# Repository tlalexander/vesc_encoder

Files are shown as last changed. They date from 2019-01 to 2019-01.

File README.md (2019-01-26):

# vesc_encoder
An openly licensed magnetic encoder board, compatible with VESC 4.12 based designs.

The data in this repository is licensed CC0, which generally means "Public Domain".
https://creativecommons.org/publicdomain/zero/1.0/

In other words: this information can be used for any purpose.

# Screenshots

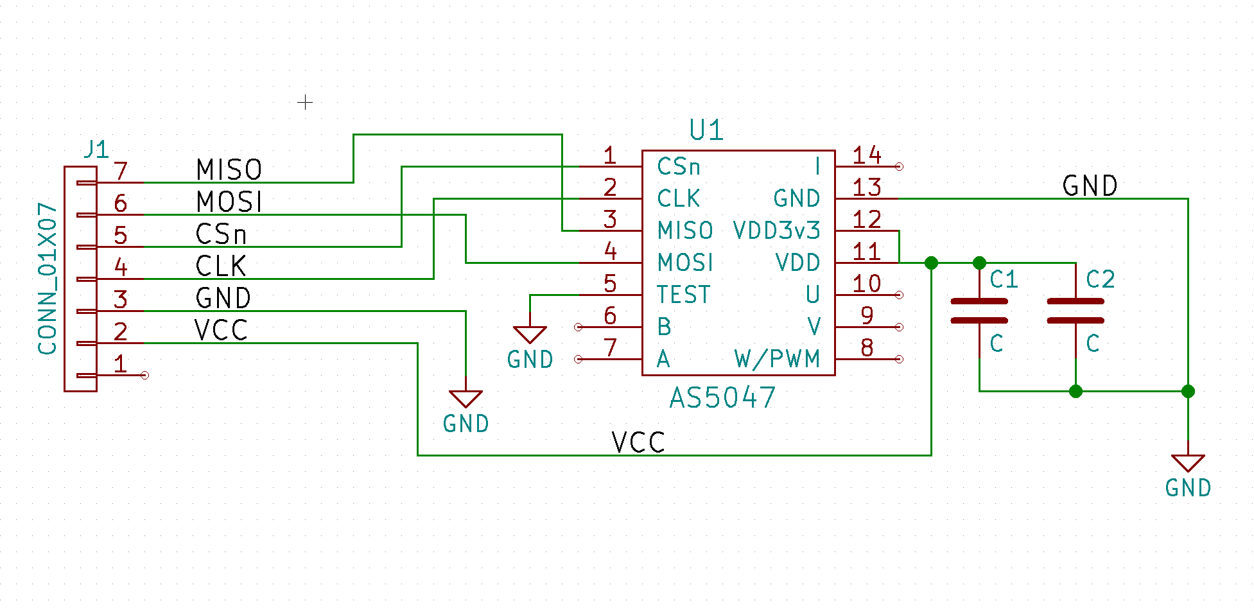
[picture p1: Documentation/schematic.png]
Image of Schematic Schematic

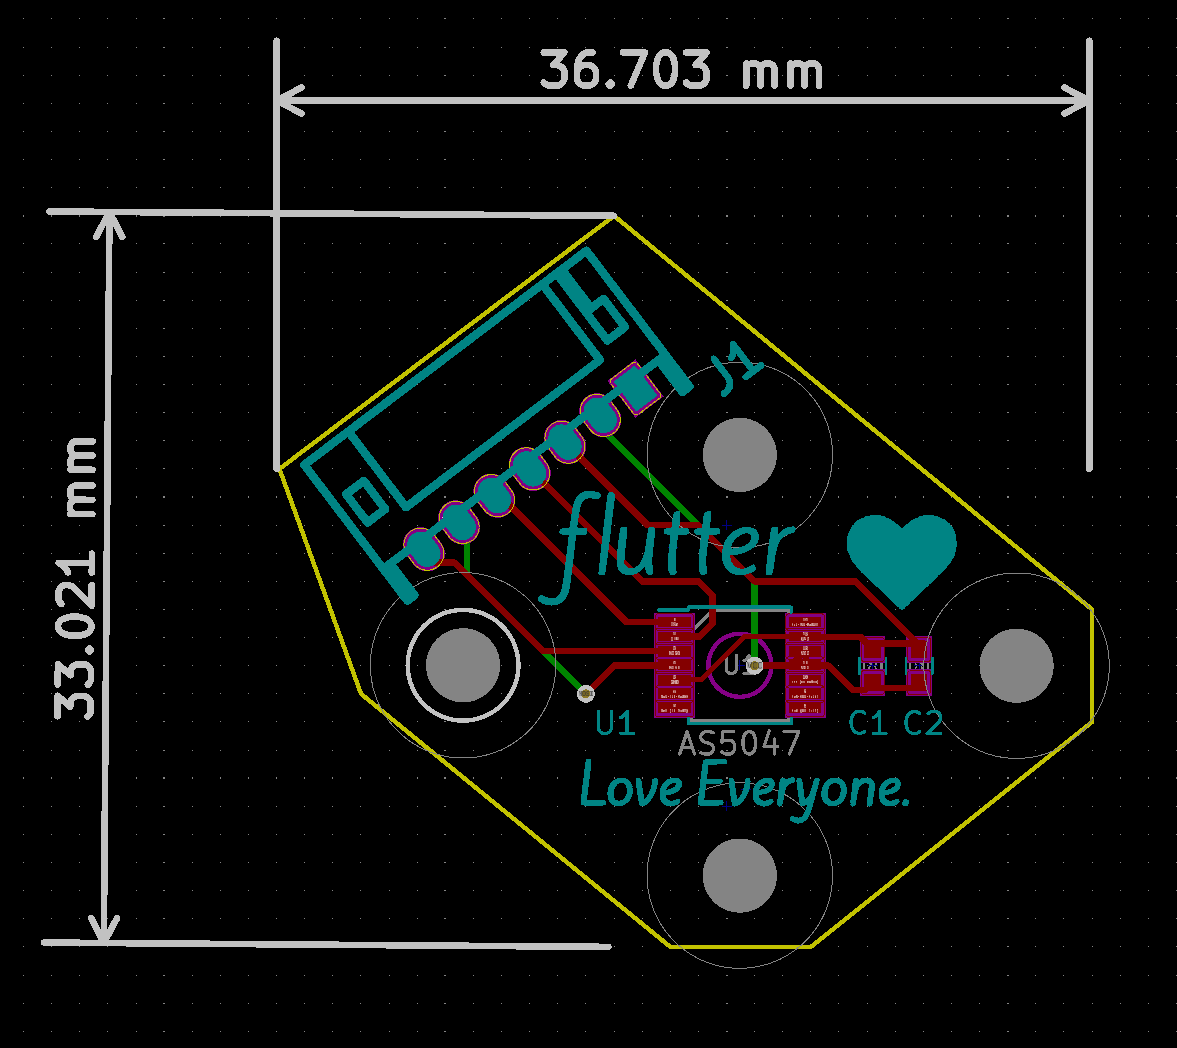
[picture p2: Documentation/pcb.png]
Image of PCB PCB

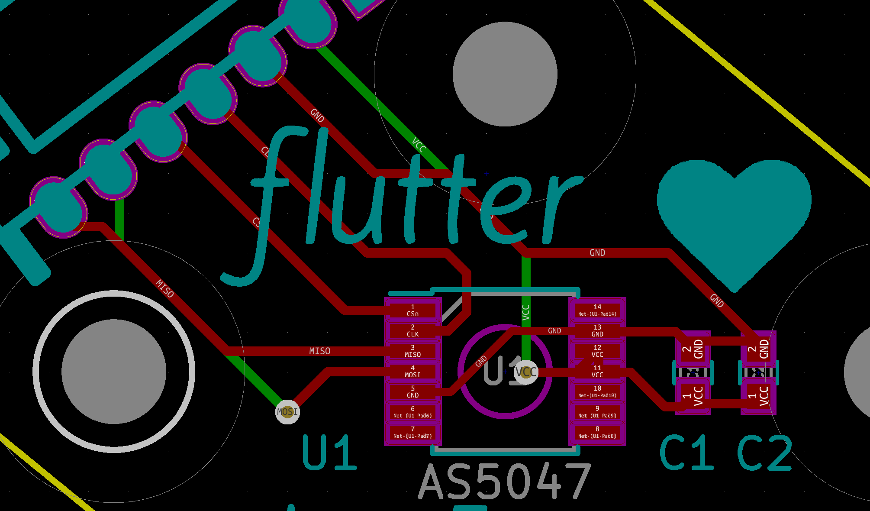
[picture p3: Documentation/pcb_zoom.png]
Image of PCB zoomed PCB Close


# Use
These files are made for KiCAD and an AS5047 encoder.

You'll need to use a firmware file with the "Use Hardware SPI" option enabled at compile time using the #defines in the config files.

# External links
See others who have used this encoder chip:
http://www.electric-skateboard.builders/t/my-vesc-with-as5047-sensor-setup/6568

And documentation on how I use it:
https://reboot.love/t/vesc-mods-for-robotics-use/

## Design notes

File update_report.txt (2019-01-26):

Info: Backing up file “/home/taylor/PCB/vesc_encoder/sym-lib-table” to file “/home/taylor/PCB/vesc_encoder/rescue-backup/sym-lib-table-2019-01-26-11-34-58”.
Info: Backing up file “/home/taylor/PCB/vesc_encoder/AS5047_encoder.sch” to file “/home/taylor/PCB/vesc_encoder/rescue-backup/AS5047_encoder-2019-01-26-11-34-58.sch”.
Info: Backing up file “/home/taylor/PCB/vesc_encoder/AS5047_encoder.pro” to file “/home/taylor/PCB/vesc_encoder/rescue-backup/AS5047_encoder-2019-01-26-11-34-58.pro”.
Info: Backing up file “/home/taylor/PCB/vesc_encoder/AS5047_encoder-cache.lib” to file “/home/taylor/PCB/vesc_encoder/rescue-backup/AS5047_encoder-cache-2019-01-26-11-34-58.lib”.
Info: Backing up file “/home/taylor/PCB/vesc_encoder/AS5047_encoder-rescue.lib” to file “/home/taylor/PCB/vesc_encoder/rescue-backup/AS5047_encoder-rescue-2019-01-26-11-34-58.lib”.
Info: Backing up file “/home/taylor/PCB/vesc_encoder/AS5047_encoder-rescue.dcm” to file “/home/taylor/PCB/vesc_encoder/rescue-backup/AS5047_encoder-rescue-2019-01-26-11-34-58.dcm”.
Info: Adding library “AS5047_encoder-rescue”, file “${KIPRJMOD}/AS5047_encoder-rescue.lib” to project symbol library table.
Info: Adding library “as5047”, file “${KIPRJMOD}/as5047.lib” to project symbol library table.
Info: Adding library “crf_1”, file “/home/taylor/PCB/bldc-hardware/design/Libraries/crf_1.lib” to project symbol library table.
Info: Adding library “BLDC_4-cache”, file “/home/taylor/PCB/bldc-hardware/design/BLDC_4-cache.lib” to project symbol library table.
Symbol “AS5047” mapped to symbol library “as5047”.
Symbol “C” mapped to symbol library “AS5047_encoder-rescue”.
Symbol “C” mapped to symbol library “AS5047_encoder-rescue”.
Symbol “GND” mapped to symbol library “power”.
Symbol “CONN_01X07” mapped to symbol library “BLDC_4-cache”.
Symbol “GND” mapped to symbol library “power”.
Symbol “GND” mapped to symbol library “power”.
Info: Symbol library table mapping complete!

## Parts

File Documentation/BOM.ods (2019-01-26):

 | Vesc Encoder BOM
 | Designator | Description | Value | Digikey PN | Manufacturer | Manuf. PN | QTY
 | J1 | CONN HEADER PH SIDE 7POS 2MM | 7 pin side exit | 455-1724-ND | JST | S7B-PH-K-S(LF)(SN) | 1
 | C1 | CAP CER 0.1UF 10V X7R 0603 | 0.1UF 10V | 399-1095-1-ND | KEMET | C0603C104K8RACTU | 1
 | C2 | CAP CER 1UF 10V X5R 0603 | 1UF 10V | 399-3118-1-ND | KEMET | C0603C105K8PACTU | 1
 | U1 | AS5047 |  |  | AMS
 | For PCB Fab orders, Also Fab 1 cable with the following specifications:
 | Connector A | Wires | Connector B
Digikey | 455-1161-ND | Straight through (x7), black, 8” long | Same as Connector A
Desc. | 7 Pin JST PH
MFR | JST
MFR PN | PHR-7
 | In other words, please make a JST PH 7 pin cable with connectors on both ends, wired pin 1 to 1, 2 to 2, etc…

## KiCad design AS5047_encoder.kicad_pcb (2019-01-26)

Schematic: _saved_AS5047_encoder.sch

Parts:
C1, C2: C; C_0603
J1: CONN_01X07; s7b-ph-kl
U1: AS5047; TSSOP-14_4.4x5mm_Pitch0.65mm

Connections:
/CLK: J1.4, U1.2
/CSn: J1.5, U1.1
/MISO: J1.7, U1.3
/MOSI: J1.6, U1.4
/VCC: C1.1, C2.1, J1.2, U1.11, U1.12
GND: C1.2, C2.2, J1.3, U1.5, U1.13

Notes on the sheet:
Author: Taylor Alexander, Jan 2018. VESC Compatible encoder board, Rev 1.0. This encoder board can be used with a radially polarized magnet to sense the position of a shaft. Typically used for motor encoders and works great for smooth starts or robotics prototyping. VESC fans will appreciate that t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

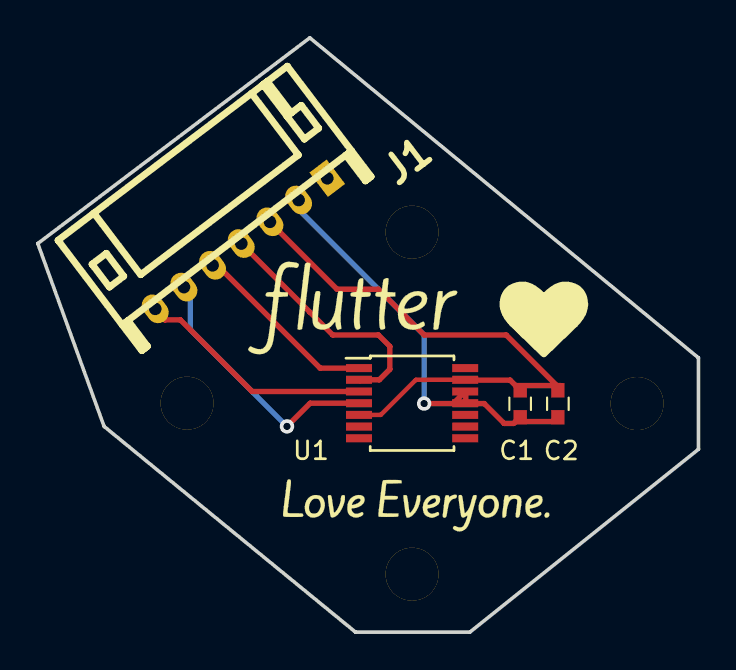
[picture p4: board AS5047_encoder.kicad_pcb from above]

Board: 2 copper layers, 36.7 x 33.0 mm, 4 parts (0 on the bottom side), 6 nets.

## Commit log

2018-01-09 Change connector and update component associations.
    [AS5047_encoder.kicad_pcb, AS5047_encoder.sch]
2018-01-17 Fixed outline. Generated gerbers. Added BOM. Ordered a batch of boards.
    [AS5047_encoder-B.Cu.gbl, AS5047_encoder-B.Mask.gbs, AS5047_encoder-B.Paste.gbp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]
2019-01-26 Imported to a new Kicad install and removed remnant traces from PCB layout. Suggest re-export gerbers to remove benign extra trace.
    [AS5047_encoder-2019-01-26-11-34-58.sch, AS5047_encoder.kicad_pcb, BOM.ods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]

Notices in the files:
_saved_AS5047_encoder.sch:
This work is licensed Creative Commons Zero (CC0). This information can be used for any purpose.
